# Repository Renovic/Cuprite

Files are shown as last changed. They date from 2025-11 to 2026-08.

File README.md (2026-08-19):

# Cuprite

160mm^3 High speed corexy

Cuprite_V2_2026-Jun-14_01-05-33AM-000_CustomizedView40187612621_png



* [Design Components](#design-components)
* [Design Reasoning](#why-did-i-design-this)
* [BOM](<BOM.csv>)
* [Graphs](#graphs)

## Files
- [CAD (F3Z)](CAD/Cuprite.f3z)
- [CAD (STEP)](CAD/Cuprite.step)
- [PCB Gerbers](PCB/Cuprite_ADXL_gerbers.zip)
- [BOM](<BOM.csv>)

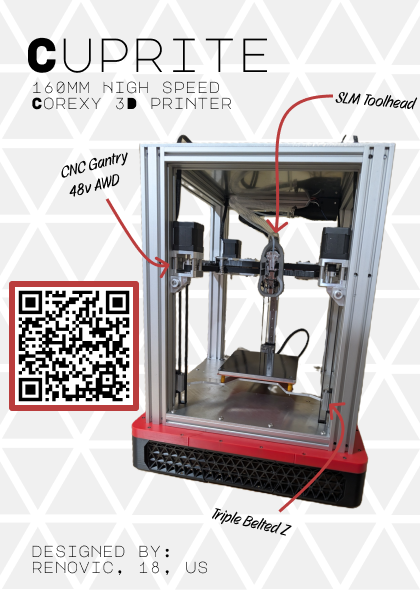
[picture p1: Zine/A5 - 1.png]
A5 - 1


### Sponsors
* [Hack Club (Fallout)](https://fallout.hackclub.com/) 
* [Sunlu](https://www.sunlu.com/)
* [OSHWLAB(JLCPCB)](https://oshwlab.com/activities/stars)
* [LDO](https://ldomotion.com/)
* [BST Automation](https://www.bstautomation.com/)
* [Filastruder](https://www.filastruder.com/)

## Design Components
- Fast and Rigid Corexy Gantry
  * Monolith Inspired gantry
  * 12mm AWD using 2504 s55 nema 17s, with 48V
  * Full cnc components for rigidity and reduced mass
- Solid Frame
  * 4040 verticals and 2040/4040 horizontals
  * 5mm structural aluminum panels
- Triple Z Axis
  * Triple Nema 17 G2Z
  * 9mm Belts
  * Maxwell motion coupling for accurate bed leveling (Inspired by ANNEX K3 Z)
- Rigid Toolhead 
  * CNC and SLM toolhead
  * Custom hotend for a cheap long meltzone (~55mm)
  * Center of mass optimized
  * Duct design aided by CFD
- Aesthetic panels
  * Parametric Kumiko panels that allow for customizability
  * Covers up 1/2" of PIR insulation
  * Integrates an extrusion based door

## Why did I design this?
The original concept for Cuprite was an extremely high speed corexy that focused on rigidity and made as little comrpromises as possible. Other than the build volume and size. Surprisingly, it's larger than a P1S while having a 100mm smaller bed.

The original one was a rushed design that happened in 2 weeks last summer, but it taught me a lot about printer design and I managed to get some sponsors. Now, I'm incorporating everything I've learned about good 3d printer design. 

Also, I thought the original was a bit boring with plain aluminum panels.

## What could you use from this project?
My build is pretty unique, so I dont expect people to build a similar printer, however you could utilize multiple aspects from it:
- The toolhead is afaik the most compact com optimized toolhead with a 50mm long meltzone. It about 10mm shorter than other similar toolheads.
- Kumiko panels is parametric, so you can use it on a lot of printers (not that reliable, so you might need to ask me for help with specific configurations)
- G2Z drives and Z joints. Normally G2Z drives are used on v2s or microns, but not that often on trident-like printers
- You could use my gantry since it supports 12mm belts (Monolith cnc gantry is a great option otherwise)

## Wiring?
The LDO leviathan + extension board has enough ports for all of the components, so its simply pluging into the correct ports. The only other wiring is ssrs for heatbed and chamber heater.

## Graphs




## Inspiration/References:
- Monolith Gantry: https://github.com/Monolith3D/Monolith_Gantry
- Paper View's Kumiko Panels: https://makerworld.com/en/models/1614814-large-kumiko-frame-generator#profileId-1733448
- DK's toolhead: https://github.com/Kizime123/DKs-Monolith-Toolhead
- DDerg's cnc joints: https://github.com/dderg (no project link)
- Galileo2: https://github.com/JaredC01/Galileo2
- Scarecrow for fan information and CAD: https://github.com/Thescarecow/130K-RPM-28mm-ducted-fan-Cad-COM
- Hex-Zero for Z tensioner: https://github.com/Alexander-T-Moss/Hex-Zero
- Chamber Heater Mount: https://github.com/GiulianoM/PTC_Heater_Mount
- ADXL: https://github.com/xbst/KUSBA-PRO
- LED Strip Holder: https://www.printables.com/model/84735-led-strip-holder-for-voron-24
- Also big thanks to anyone who provided feedback on any of my designs

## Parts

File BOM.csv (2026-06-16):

Category | Have/Exclude | Component / Item | Qty | Est. USD | Est. Total | Notes | Sources |  | Additional Notes
Filament
Filament | TRUE | Sunlu Black ABS | 2 |  |  | Sponsored by Sunlu
Filament | TRUE | Sunlu Red ABS | 1 |  |  | Sponsored by Sunlu
Category | Have/Exclude | Component / Item | Qty | Est. USD | Est. Total | Notes | Sources |  | Additional Notes
Frame
T-Slot | FALSE | 4040 460mm | 4 | $12.65 | $50.60 |  | https://us.misumi-ec.com/vona2/detail/110302684530/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
T-Slot | FALSE | 4040 290mm | 4 | $8.19 | $32.76 |  | https://us.misumi-ec.com/vona2/detail/110302684530/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
T-Slot | FALSE | 2040 290mm | 6 | $5.75 | $34.50 |  | https://us.misumi-ec.com/vona2/detail/110302684350/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
T-Slot | FALSE | 2020 160mm | 1 | $4.93 | $4.93 |  | https://us.misumi-ec.com/vona2/detail/110302683830/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
T-Slot | FALSE | 2020 250mm | 1 | $4.93 | $4.93 |  | https://us.misumi-ec.com/vona2/detail/110302683830/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
T-Slot | TRUE | 2020 460mm | 2 |  | $0.00 |  | https://us.misumi-ec.com/vona2/detail/110302683830/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
T-Slot | TRUE | 2020 290mm | 2 |  | $0.00 |  | https://us.misumi-ec.com/vona2/detail/110302683830/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
T-Slot | FALSE | 2010 330mm | 2 | $6.22 | $12.44 | https://www.aliexpress.us/item/3256805640390934.html
Aluminum Panels | FALSE | Structural Panels | 5 | $43.02 | $215.12 | 50% off from OSHCUT incl shipping |  | https://app.oshcut.com/cart/O-096f8b5f-96be-4d21-93b8
Panels | FALSE | Acrylic Panels | 3 | $51.46 | $154.37 | JLC | https://jlccnc.com/cnc-machining-quote
Insulation | FALSE | PIR Foam | 1 | $14.15 | $14.15 |  | https://www.menards.com/main/building-materials/insulation/foam-board-insulation/johns-manville-4-x-8-foil-faced-polyiso-foam-board-insulation/90034729/p-1444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
Rubber Feet | FALSE | Rubber Feet 28 x 22 x 16.5mm | 4 | $0.98 | $3.90 |  | https://www.aliexpress.us/item/2255800401618330.html?curPageLogUid=PIKSxm5qJwdM
Foam Tape | FALSE | Neoprene Rubber Strip | 1 | $3.21 | $3.21 |  | https://www.aliexpress.us/item/3256805075652387.html
Category | Have/Exclude | Component / Item | Qty | Est. USD | Est. Total | Notes | Sources |  | Additional Notes
Gantry
Rails | TRUE | Mgn 12 220mm | 1 |  |  | Sponsored by BST
Rails | TRUE | Mgn 9 210mm | 2 |  |  | Sponsored by BST
Tube | FALSE | 2020x3mm 250mm Tube | 1 | $14.60 | $14.60 |  | https://www.aliexpress.us/item/3256808551971726.html?curPageLogUid=GSkYAb7nQiv1
Motors | TRUE | 2504 s55 | 4 | $28.00 | $0.00 | Sponsored by LDO | https://kb-3d.com/store/stepper-motors-servos/2604-ldo-stepper-motor-high-temp-nema-17-42sth48-2504ah-s55-speedy-power-1651971790699.html
Belt | FALSE | 12mm belt 2.4M | 1 | $18.99 | $18.99 |  | https://diodekingsupply.com/products/gates-power-grip-gt2-epdm-belt-2-4-meter-closed-loop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 |  | 1121mm for 1 belt length
Pulleys | FALSE | Gt2 20t 12mm | 8 | $3.47 | $27.78 |  | https://www.aliexpress.us/item/2251832836965041.html
Pulleys | FALSE | Gt2 20t 6mm | 4 | $3.06 | $12.23 |  | https://www.aliexpress.us/item/2251832836965041.html
Bearings | FALSE | f605 | 20 | $0.37 | $7.40 | JLC | https://jlcmc.com/product/b/C15/BR8366/deep-groove-ball-bearings-with-flange-types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
Bearings | FALSE | 605 bearing | 6 | $0.15 | $0.91 | JLC | https://jlcmc.com/product/b/C15/BR8364/deep-groove-ball-bearing-double-side-with-dust-cover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
Bearings | FALSE | f695 | 4 | $0.20 | $0.80 | JLC | https://jlcmc.com/product/b/C15/BR8366/deep-groove-ball-bearings-with-flange-types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
Spacer | FALSE | M3xD6x20mm | 14 | $0.51 | $7.15 |  | https://www.aliexpress.us/item/3256807676471039.html
Spacer | FALSE | M5xD8x5mm | 20 | $0.20 | $4.03 |  | https://www.aliexpress.us/item/3256807676471039.html
Pin | FALSE | M3xD6x35mm | 6 | $0.74 | $4.44 |  | https://www.aliexpress.us/item/3256803877489650.html
Pin | FALSE | 5mmx40mm | 4 | $0.71 | $2.85 |  | https://www.aliexpress.us/item/3256806837028480.html
Shims | FALSE | 0.5mm 5ID | 16 | $0.12 | $1.94 |  | https://www.aliexpress.us/item/3256801859874107.html
Shims | FALSE | 1mm 5ID | 6 | $0.35 | $2.11 |  | https://www.aliexpress.us/item/3256801859874107.html
Spring | FALSE | 6mm OD 9mm Length | 4 | $0.33 | $1.32 | JLC | https://www.aliexpress.us/item/3256805126221346.html?gatewayAdapt=glo2usa4itemAdapt
CNC parts | FALSE | Rear Motor Mounts | 4 | $26.52 | $106.08 | JLC | https://jlccnc.com/cnc-machining-quote
CNC parts | FALSE | Front Motor Mounts | 4 | $25.61 | $102.42 | JLC | https://jlccnc.com/cnc-machining-quote
CNC parts | FALSE | Tensioners | 2 | $17.54 | $35.08 | JLC | https://jlccnc.com/cnc-machining-quote
CNC parts | FALSE | XY Joints | 4 | $32.47 | $129.88 | JLC | https://jlccnc.com/cnc-machining-quote
Category | Have/Exclude | Component / Item | Qty | Est. USD | Est. Total | Notes | Sources |  | Additional Notes
Toolhead
Heater | FALSE | STDv6 Heaters | 1 | $19.43 | $19.43 |  | https://trianglelab.net/products/std6?VariantsId=11907
Heat Break | FALSE | E3 S1 Bimetallic heatbreak | 1 | $5.70 | $5.70 |  | https://www.aliexpress.us/item/3256805790699617.html
CPAP | FALSE | 130k RPM Fan | 1 | $13.86 | $13.86 |  | https://www.aliexpress.us/item/3256808315658138.html?gatewayAdapt=glo2usa4itemAdapt
CPAP | FALSE | CPAP Tube | 1 | $7.00 | $7.00 |  | https://www.ebay.com/itm/197951054068?itmmeta=01KSKRKVPZHTJWCMN59X1VYEBX
Gears | FALSE | K1 gearset | 1 | $9.07 | $9.07 |  | https://www.aliexpress.us/item/3256808414846514.html
Motor | TRUE | Nema 14 | 1
Bearing | FALSE | 624ZZ | 1 | $0.10 | $0.10 | JLC | https://jlcmc.com/product/b/C15/BR8364/deep-groove-ball-bearing-double-side-with-dust-cover
Bearing | FALSE | Mr84zz | 10 | $1.01 | $10.06 |  | https://www.aliexpress.us/item/3256809175647670.html
SLM Parts | FALSE | Heatblock brace | 1 | $11.90 | $11.90
SLM Parts | FALSE | Ducts | 1 | $31.56 | $31.56
SLM Parts | FALSE | Belt Clamp | 2 | $4.00 | $8.00
SLM Parts | FALSE | Belt Clip | 2 | $4.00 | $8.00
CNC Parts | FALSE | Center Block | 1 | $86.06 | $86.06 | JLC | https://jlccnc.com/cnc-machining-quote
CNC Parts | FALSE | Extruder Housing | 1 | $39.21 | $39.21 | JLC | https://jlccnc.com/cnc-machining-quote
CNC Parts | FALSE | Hotend Block | 1 | $50.21 | $50.21 | JLC | https://jlccnc.com/cnc-machining-quote
CPAP | FALSE | Hose Clamps | 10 | $0.19 | $1.87 |  | https://www.aliexpress.us/item/3256807343760250.html
Category | Have/Exclude | Component / Item | Qty | Est. USD | Est. Total | Notes | Sources |  | Additional Notes
Z axis
Rails | TRUE | MGN12H 200mm | 3 |  |  | Sponsored by BST
Bed | TRUE | 160mm SaladFork Bed | 1
Heater | FALSE | JLC Flex heater | 1 | $20.01 | $20.01 | JLC | https://flexheater.jlcpcb.com/quote
G2z | FALSE | G2z Kits | 2 | $39.99 | $79.98 | Filastruder
Belt | FALSE | 9mm 2m | 1 | $23.80 | $23.80 | Filastruder | https://www.filastruder.com/collections/gates/products/gates-2gt-belts-high-temperature-epdm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
Pulley | FALSE | 20t Gt2 9mm Pulley 8mm ID | 3 | $5.64 | $16.92 |  | https://www.aliexpress.us/item/2255800930086012.html
Pin | FALSE | 8x45mm M5 | 3 | $1.72 | $5.16 | JLC | https://jlcmc.com/product/s/B08/BACD/linear-shaft-solid-straight-one-end-with-internal-thread-g6-tolerance
Spring | TRUE | Bed Springs | 3
Bearing | FALSE | MR148ZZ | 6 | $0.18 | $1.11 | JLC | https://jlcmc.com/product/b/C15/BR8364/deep-groove-ball-bearing-double-side-with-dust-cover
Shims | FALSE | 0.5mm 8ID | 9 | $0.24 | $2.17 |  | https://www.aliexpress.us/item/3256801859874107.html?mp=1
SLM Parts | FALSE | Belt Clamp | 3 | $4.00 | $12.00 |  | https://jlc3dp.com/3d-printing-quote
SLM Parts | FALSE | Z Joints | 3 | $11.05 | $33.15 | JLC | https://jlc3dp.com/3d-printing-quote
CNC Parts | FALSE | Z Idlers | 3 | $21.68 | $65.04 | JLC | https://jlccnc.com/cnc-machining-quote
Category | Have/Exclude | Component / Item | Qty | Est. USD | Est. Total | Notes | Sources |  | Additional Notes
Kumiko Panels
Magnets | TRUE | 6x3mm | 12
Pin | TRUE | 5mm x100mm | 1 | $1.52 | $0.00
Pin | FALSE | 5mm x 50mm | 2 | $1.69 | $3.38 | JLC | https://jlcmc.com/product/s/B08/BACA/linear-shaft-solid-straight-g6-tolerance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
Bushing | FALSE | 9x8mm Bushing 5ID | 6 | $0.79 | $4.71 | JLC | https://jlcmc.com/product/s/B01/BWYA/oil-free-bushing-special-bronze-straight-column-inner-diameter-tolerance-f7-e7-outer-diameter-tolerance-m6-r6
Shim | TRUE | 0.5mm shim 5ID | 6
Category | Have/Exclude | Component / Item | Qty | Est. USD | Est. Total | Notes | Sources |  | Additional Notes
Fasteners
BHCS | FALSE | M5x45 BHCS | 4 | $0.16 | $0.66 | JLC | https://jlcmc.com/product/s/E02/EDLG/iso-7380-hex-socket-button-head-screw
BHCS | FALSE | M5x40 BHCS | 6 | $0.09 | $0.52 | JLC | https://jlcmc.com/product/s/E02/EDLG/iso-7380-hex-socket-button-head-screw
BHCS | FALSE | M5x30 BHCS | 8 | $0.04 | $0.34 | JLC | https://jlcmc.com/product/s/E02/EDLG/iso-7380-hex-socket-button-head-screw
BHCS | FALSE | M5x16 BHCS | 32 | $0.03 | $0.83 | JLC | https://jlcmc.com/product/s/E02/EDLG/iso-7380-hex-socket-button-head-screw
BHCS | FALSE | M5x10 BHCS | 87 | $0.02 | $1.48 | JLC | https://jlcmc.com/product/s/E02/EDLG/iso-7380-hex-socket-button-head-screw
BHCS | FALSE | M5x8 BHCS | 55 | $0.02 | $1.01 | JLC | https://jlcmc.com/product/s/E02/EDLG/iso-7380-hex-socket-button-head-screw
BHCS | FALSE | M4x20 BHCS | 8 | $0.02 | $0.16 | JLC | https://jlcmc.com/product/s/E02/EDLG/iso-7380-hex-socket-button-head-screw
BHCS | FALSE | M4x8 BHCS | 4 | $0.02 | $0.09 | JLC | https://jlcmc.com/product/s/E02/EDLG/iso-7380-hex-socket-button-head-screw
BHCS | FALSE | M3x25 BHCS | 32 | $0.01 | $0.46 | JLC | https://jlcmc.com/product/s/E02/EDLG/iso-7380-hex-socket-button-head-screw
BHCS | FALSE | M3x20 BHCS | 16 | $0.01 | $0.19 | JLC | https://jlcmc.com/product/s/E02/EDLG/iso-7380-hex-socket-button-head-screw
BHCS | FALSE | M3x12 BHCS | 16 | $0.01 | $0.12 | JLC | https://jlcmc.com/product/s/E02/EDLG/iso-7380-hex-socket-button-head-screw
BHCS | FALSE | M3x10 BHCS | 32 | $0.01 | $0.23 | JLC | https://jlcmc.com/product/s/E02/EDLG/iso-7380-hex-socket-button-head-screw
BHCS | FALSE | M3x8 BHCS | 35 | $0.01 | $0.20 | JLC | https://jlcmc.com/product/s/E02/EDLG/iso-7380-hex-socket-button-head-screw
BHCS | FALSE | M3x6 BHCS | 63 | $0.01 | $0.33 | JLC | https://jlcmc.com/product/s/E02/EDLG/iso-7380-hex-socket-button-head-screw
SHCS | FALSE | M5x45 SHCS | 4 | $0.11 | $0.44 | JLC | https://jlcmc.com/product/s/E02/EDLA/din-912-gb-t-70.1-standard-socket-head-cap-screws-full---half-thread
SHCS | FALSE | M4x12 SHCS | 6 | $0.02 | $0.12 | JLC | https://jlcmc.com/product/s/E02/EDLA/din-912-gb-t-70.1-standard-socket-head-cap-screws-full---half-thread
SHCS | FALSE | M3x45 SHCS | 14 | $0.04 | $0.57 | JLC | https://jlcmc.com/product/s/E02/EDLA/din-912-gb-t-70.1-standard-socket-head-cap-screws-full---half-thread
SHCS | FALSE | M3x40 SHCS | 3 | $0.07 | $0.21 | JLC | https://jlcmc.com/product/s/E02/EDLA/din-912-gb-t-70.1-standard-socket-head-cap-screws-full---half-thread
SHCS | FALSE | M3x35 SHCS | 2 | $0.05 | $0.09 | JLC | https://jlcmc.com/product/s/E02/EDLA/din-912-gb-t-70.1-standard-socket-head-cap-screws-full---half-thread
SHCS | FALSE | M3x30 SHCS | 12 | $0.03 | $0.34 | JLC | https://jlcmc.com/product/s/E02/EDLA/din-912-gb-t-70.1-standard-socket-head-cap-screws-full---half-thread
SHCS | FALSE | M3x20 SHCS | 64 | $0.02 | $1.17 | JLC | https://jlcmc.com/product/s/E02/EDLA/din-912-gb-t-70.1-standard-socket-head-cap-screws-full---half-thread
SHCS | FALSE | M3x16 SHCS | 4 | $0.02 | $0.10 | JLC | https://jlcmc.com/product/s/E02/EDLA/din-912-gb-t-70.1-standard-socket-head-cap-screws-full---half-thread
SHCS | FALSE | M3x12 SHCS | 4 | $0.02 | $0.08 | JLC | https://jlcmc.com/product/s/E02/EDLA/din-912-gb-t-70.1-standard-socket-head-cap-screws-full---half-thread
SHCS | FALSE | M3x10 SHCS | 20 | $0.01 | $0.22 | JLC | https://jlcmc.com/product/s/E02/EDLA/din-912-gb-t-70.1-standard-socket-head-cap-screws-full---half-thread
SHCS | FALSE | M3x8 SHCS | 8 | $0.01 | $0.11 | JLC | https://jlcmc.com/product/s/E02/EDLA/din-912-gb-t-70.1-standard-socket-head-cap-screws-full---half-thread
FHCS | FALSE | M3x25 FHCS | 50 | $0.01 | $0.70 | JLC | https://jlcmc.com/product/s/E02/EDLJ/din-7991-gb-t-70.3-hex-socket-countersunk-head-screw
FHCS | FALSE | M3x20 FHCS | 32 | $0.01 | $0.35 | JLC | https://jlcmc.com/product/s/E02/EDLJ/din-7991-gb-t-70.3-hex-socket-countersunk-head-screw
FHCS | FALSE | M3x10 FHCS | 6 | $0.01 | $0.04 | JLC | https://jlcmc.com/product/s/E02/EDLJ/din-7991-gb-t-70.3-hex-socket-countersunk-head-screw
FHCS | FALSE | M3x8 FHCS | 9 | $0.01 | $0.06 | JLC | https://jlcmc.com/product/s/E02/EDLJ/din-7991-gb-t-70.3-hex-socket-countersunk-head-screw
FHCS | FALSE | M3x6 FHCS | 16 | $0.00 | $0.07 | JLC | https://jlcmc.com/product/s/E02/EDLJ/din-7991-gb-t-70.3-hex-socket-countersunk-head-screw
Low profile SHCS | FALSE | M3x8 SHCS Low | 2 | $0.79 | $1.59 | JLC | https://jlcmc.com/product/s/E02/EDLZ/hex-socket-cap-screw-ultra-short-head-type
Shoulder Bolt | FALSE | M3 D4x12 Shoulder | 2 | $0.00 | #REF! | JLC
Set Screw | FALSE | M2.5x2.5 set screw | 1 | $0.09 | $0.09 | JLC | https://jlcmc.com/product/s/E02/EDLR/din-913-914-915-916-hex-socket-set-screw-(flat-cone-cup-point-end)
Set Screw | FALSE | M4x4 set screw | 1 | $0.01 | $0.01 | JLC | https://jlcmc.com/product/s/E02/EDLR/din-913-914-915-916-hex-socket-set-screw-(flat-cone-cup-point-end)
Set Screw | FALSE | M4x3 set screw | 8 | $0.01 | $0.05 | JLC | https://jlcmc.com/product/s/E02/EDLR/din-913-914-915-916-hex-socket-set-screw-(flat-cone-cup-point-end)
Heatset | FALSE | M3 Heatset | 70 | $0.07 | $4.70 |  | https://www.aliexpress.us/item/3256805885174058.html
Hex Nut | FALSE | M5 Hex nut | 8 | $0.11 | $0.91 | JLC | https://jlcmc.com/product/s/E04/EMLC/anti-loosening-nut
Hex Nut | TRUE | M4 Hex nut | 6 | $0.00 | $0.00 | JLC | https://jlcmc.com/product/s/E04/EMLC/anti-loosening-nut
Hex Nut | TRUE | M3 Hex nut | 58 | $0.00 | $0.00 |  | https://jlcmc.com/product/s/E04/EMLC/anti-loosening-nut
Hex Nut | FALSE | M3 Hex nut (lock) | 9 | $0.15 | $1.38 | JLC | https://jlcmc.com/product/s/E04/EMLC/anti-loosening-nut
T Nut | FALSE | M5 T nut | 102 | $0.06 | $6.61 | JLC | https://jlcmc.com/product/s/T02/TPAB/m3-m4-m5-roll-in-t-slot-nut-with-ball-spring-for-20-series-aluminum-profiles
T Nut | FALSE | M3 T nut | 82 | $0.07 | $5.39 | JLC | https://jlcmc.com/product/s/T02/TPAB/m3-m4-m5-roll-in-t-slot-nut-with-ball-spring-for-20-series-aluminum-profiles
Washer | FALSE | M5 | 100 | $0.00 | $0.29 | JLC | https://jlcmc.com/product/s/E06/EPDA/flat-washer-level-a
Category | Have/Exclude | Component / Item | Qty | Est. USD | Est. Total | Notes | Sources |  | Additional Notes
Electronics
Mainboard | TRUE | LDO leviathan | 1 |  |  | Sponsored by LDO
Mainboard | FALSE | LDO leviathan Expansion | 1 |  |  | Sponsored by LDO
SBC | FALSE | RPI 5 1gb | 1 | $42.99 | $42.99 |  | https://www.microcenter.com/product/704295/raspberry-pi-5
PSU | TRUE | 24V 200W | 1 |  | $0.00
PSU | FALSE | 48V 200W | 1 | $26.99 | $26.99 | Filastruder | https://www.filastruder.com/collections/power-supplies/products/meanwell-lrs-200-48-psu
Fans | FALSE | 6025 fans | 8 | $1.70 | $13.58 | JLC
Fans | FALSE | 6015 fans | 2 | $6.89 | $13.78 |  | https://www.aliexpress.us/item/2251832744094136.html
Fans | FALSE | 8038 fans | 2 | $2.99 | $2.99 | Filastruder | https://www.filastruder.com/products/nmb-technologies-08038ra-24s-ea-axial-fan-24vdc-1-75a-42w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
SSR | TRUE | SSR | 2 | $34.00 | $0.00 | Free from TE | https://www.te.com/en/product-1-2323802-1.html
Heater | FALSE | PTC Heater | 1 | $17.90 | $17.90 |  | https://www.amazon.com/Precision-Constant-Temperature-Electric-Humidifier/dp/B07P5NCR2F/
LEDs | FALSE | 24V 2835 | 1 | $7.28 | $7.28 |  | https://www.aliexpress.us/item/3256802169002555.html?curPageLogUid=aFKuQChHYUUk
Wires | FALSE | 22 AWG FEP wire | 4 | $2.67 | $10.68 |  | https://www.aliexpress.us/item/2251832618202013.html
Wires | FALSE | 16 AWG FEP wire | 2 | $6.49 | $12.98 |  | https://www.aliexpress.us/item/2251832618202013.html
Sleeve | FALSE | PET sleeve 4mm | 1 | $5.09 | $5.09 |  | https://www.aliexpress.us/item/2251832618202013.html
Sleeve | FALSE | PET sleeve 6mm | 1 | $6.34 | $6.34 |  | https://www.aliexpress.us/item/2251832618202013.html
Connectors | FALSE | JST XH | 1 | $4.31 | $4.31 |  | https://www.aliexpress.us/item/3256808432090471.html
Connectors | FALSE | Crimp Connectors | 1 | $7.84 | $7.84 |  | https://www.aliexpress.us/item/3256809169357323.html
Crimper | FALSE | IWISS Crimper | 1 | $19.28 | $19.28 |  | https://www.aliexpress.us/item/3256809419112769.html
 | Parts Total(Shipping Included) |  | Tax | Total
AliExpress |  | $223.76 | $17.90 | $241.66
Amazon |  | $17.90 | $1.43 | $19.33
Ebay |  | $11.00 | $0.88 | $11.88
Oshcut |  | $215.12 | $17.21 | $232.33
Misumi |  | $89.40 | $10.98 | $100.38
In3dtec |  | $103.87 | $8.31 | $112.18
Trianglelab |  | $19.43 | $1.55 | $20.98
Menards |  | $14.15 | $1.13 | $15.28
Microcenter |  | $42.99 | $3.44 | $46.43
JLCPCB(Sponsor) |  | $300.00 | $24.00 | $324.00
Filastruder (Half Sponsor) |  | $78.76 | $6.30 | $85.06
Total | $1,209.52

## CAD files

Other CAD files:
CAD/Toolhead.step
CAD/Cuprite.step
CAD/Cuprite.f3z
CAD/Toolhead.f3z

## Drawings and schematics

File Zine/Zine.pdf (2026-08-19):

# Cuprite

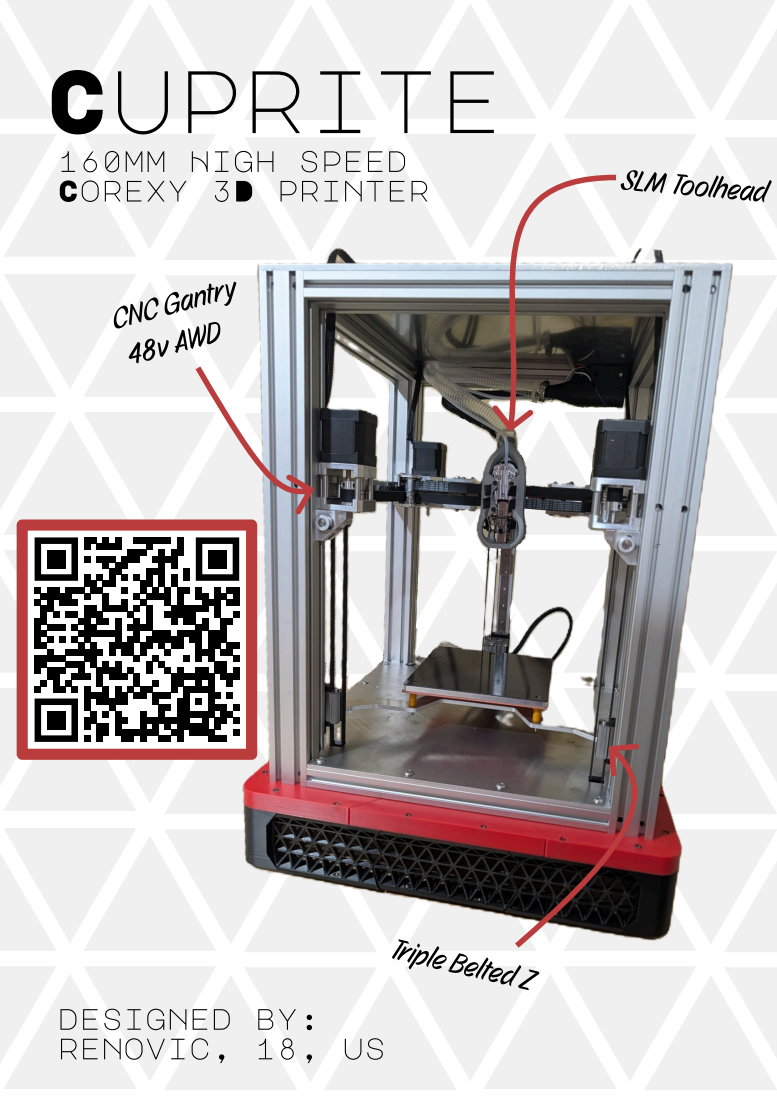
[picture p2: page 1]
CNC Gantry 48v AWD; SLM Toolhead; Triple Belted Z

160mm High speed Corexy 3D printer

designed by:
renovic, 18, us

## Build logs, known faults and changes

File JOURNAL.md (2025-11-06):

<!--
  ===================    !!READ THIS NOTICE!!   ====================
  DO NOT edit this file manually. Your changes WILL BE OVERWRITTEN!
  This journal is auto generated and updated by Hack Club Blueprint.
  To edit this file, please edit your journal entries on Blueprint.
  ==================================================================
-->

## 11/1/2025 - Intial Design Ideas, Frame, Gantry Components  

So this is a full redesign of my highway printer: 
https://github.com/Renovic/Cuprite-OLD-
Cuprite Full Printer Render(Blue)
Cuprite Electronics Render (Blue)Cuprite Toolhead Focus Render(Blue)

There are a couple of things that happened that made me want to redesign:
- Sponsors: I reached out to a couple of companies and I got some sponsors which means I needed to change a couple of parts. The companies are: LDO, Sunlu, JLCPCB(OSHWLABS), BST AUTOMATION, Filastruder
- Makerspace access: Now I have access to a makerspace and a source for sheetmetal so I have access to more manufacturing capabilities
- Better Design Ideas: My original design was rushed and wasn't ideal. For example, the toolhead COM wasn't next to the carriage, so it would lead to worse results.
- Better Aesthetics: I've gotten a lot of new ideas for improved aesthetics

# Day 1- Full Redesign Concept (Oct 1st - 3rd)
Over these few days, I consolidated my ideas on what I wanted to redesign. I also started sourcing parts for the build. 

So here are all of the changes from the old version I plan:
### Frame: 

2020 + 2040 - > 4040 verticals (JLCMC) 
- This will imporve rigidity greatly and allow for better mounting

### Insulation/Panels:

No Insulation -> 3/4" PIR Insulation
- Fits inside of the frame, which is why 4040 verticals are important

### Gantry: 

9mm belts -> 12mm EPDM (partialy sponsored by Filastruder)
2WD -> 4WD (Sponserd by LDO)
1/8" Alu sheetmetal -> CNC aluminum (JLCCNC)
2020 extrusion x-gantry -> 2030 aluminum tube
- Should allow for more rigidity
- ~30% Input Shaper gain from 9mm -> 12mm belts
- ~100% Input Shaper gain from 2WD -> AWD
- More Input Shaper gain from extra frame, and gantry rigidty

### Toolhead:

Peopoly Lancer -> Custom aluminum hotend (JLC3DP)
Fully SLM/CNC toolhead (JLC3DP & JLCNC)
G2 Extruder (LDO)
- Better extrusion from G2
- More rigidity from bottom supported hotend
- Centered COM from redesign
- higher flow rate

### Cooling:

WS7040 -> 130k RPM Ducted Fan
No flap -> Stepper motor flap 
- Cheaper
- Higher max cfm

### Z Axis

In chamber motors -> bottom-mounted motors
BMG Gear Reduction -> G2Z
3dp joints -> slm joints (JLC3DP)
No spring tension -> spring holding down bed frame to joints
Extrusion bed frame -> Laser cut aluminum frame
- More rigidity
- More travel from bottom-mounted z motors
- Better z motion consistency, and as a result better layer stacking

### Electronics

Fystec Spider -> Leviathan + Expansion board (sponsored by LDO)
tmc2209 XY motor drivers -> tmc5160 XY motor drivers (Built in to Leviathan)
24V XY -> 48V XY (Partially sponsored by Filastruder)
0 mainboard cooling -> 4x 6020 fans (JLCMC)
- Higher stepper motor speeds
- Better step control
- Can cool stepper motors

### Chamber Heater

None -> 100W Chamber Heater
- Cheap
- Allows for good chamber temps
### Aesthetic Improvements
Rear backpack -> top and bottom electronics enclosures
Exposed panels -> printed covers
Door hinges integrated into panel covers
- Displays Leviathan and good looking electronics on top
- Hides PSUs underneath
- Nicer visuals

Even with all of these improvments, the cost of new components should be cheaper than the original.

**Hours Spent: 12**
**Total: 12** 
# Day 2 - SLM Toolhead Redesign Concept (Oct 13th)
I started by designing a hotend similar to the hotend in the monolith toolhead, or DK's slm bmg toolhead. This should get high flow rates and have mounting for a bottom hotend brace.
I spent the rest of the time messing around with different extruder options, and hotend locations to find anything that could get me a good com and nice design.
The main issue was with bmg gears the gear covers the bolts mounting the main toolhead body into the mgn12h carriage. 
I also wanted to try using a g2e kit because it should give me very precise extrusion without any wood grain affect thats normally caused by double gear extruders. Although I didn't get as much as I wanted done, I was able to figure out the location of the hotend and extruder that could give me a decent center of mass, and I got some ideas of the rest of the design. 




**Hours Spent: 6**
**Total: 18** 

# Day 3 - CNC Front Motor Mounts (Oct 17th)
Main Goal for this was component was to incorperate the front extrusion brace and rigid part.
This is using the monolith belt path like before, but now for 12mm belts. 
Also I made sure to insert every fastener required so I can make sure I source all of the components and don't have any intersections. But this made it take a bit longer than how I was designed previously. 
During this day, I also found sources for the hardware required, most of the hardware like bearings, standoffs, and bolts were from JLCMC. 



**Hours Spent: 4**
**Total: 22** 

# Day 4 - New Frame & Panels (Oct 30th)
I redesigned the Frame to use 4040 verticals.
I also was able to find 3/8" aluminum panels, so I designed the aluminum panels to be mounted onto the frame.
Another thing I realized I missed on the first design is the rubber strips to reduce heat and vibration transfers from the frame to panels, so I designed those in. 
Finally I added insulation to the internal faces of the panels. 
The overall width of the printer is 50mm wider than the orignal printer, but it includes insulation.





**Hours Spent: 2.5**
**Total: 24.5* 

# Day 5 - X Axis (Oct 31st)
Today I redesigned the X axis and XY joints to use 12mm belts and 2030 Aluminum Tube. 
The XY joints are 2 part that clamp onto the mgn9h carriage and bolt into the carriage. 
Then I made the 2030 aluminum tube and mounting hardware. I also needed to add 3d printed crush blocks into the tube so I can mount the rail to the tube without worrying about bending the tube inwards. 
I also found the sources for aluminum tube, hardware and compression springs for correct spacing on the live idler joint. 







Then I wanted to see how the gantry looked, so I made a gantry assembly and put it into the frame.




**Hours Spent: 5.5**
**Total: 31**

## 11/2/2025 - Designing Rear Motor Mounts  

# Day 6 - Rear Motor Mounts (Nov 1st)
I was really confused about how to design the CNC belt tensioner for a while. But I finally had an idea to use slots to guide the tensioner, have a countersunk M3 screw to mount the tensioner bearing stack pin, and M5 bolts to clamp the tensioner in place. 

These took way longer than I expected because of the amount of hardware required for this part.







**Hours Spent: 6**
**Total: 37**  

## 11/3/2025 - Bed Assembly, Front Z drives  

# Day 7 - Bed Assembly, Front Z drives (Nov 2nd)
I started by designing the bed assembly. It uses a sheet metal carriage and some CNC components to mount the bed and 8mm rods that will be used for kinematic coupling. 



Then I designed the front Z drives that use G2Z planetary gearboxes for precise Z motion. Part of the design was making sure the part is entirely sealed so air from the chamber can't leak into the bottom electronics area. 







**Hours Spent: 6.5**
**Total: 43.5**  

## 11/5/2025 - Day 8 - Back Z drives, Tweaks to Z axis, More research  

# Day 8 - (Nov 4th)
I started with designing the rear Z drive, and this was pretty similar to the front Z drives, but mounted differently. 



Then I started thinking about how I was going to do the Z belt tensioners. Although I originally just planned on designing a belt tensioner similar to the Annex K3 z-axis tensioners, I wanted to see if there was something more compact. So I did some research and found Hex 0 had some very compact belt tensioners. 



These tensioners pressed the belt against the linear rail carriage and had one part slide to adjust tension. The Hex 0 z drives used 6mm belts and mgn7 rails, so I was a bit concerned about whether this would work. But thankfully, I found that the mgn12 rails had enough width for 9mm belts. I had to adjust the front z drive pulley location to make the belt line up with the edge of the carriage. I also added some channels for wires to come down the vertical 4040 extrusions, and go to the stepper. 



Then I went to make some tweaks to the bed carriage. I was a little concerened about the weight because I was using 3/8" thick aluminum and my original design was very beefy, so I checked and it was 400 grams. I decided to redesign it to be a little simpler and much lighter, and it ended up being 250 grams.

 



Finally, I started thinking about how I would get the most travel possible. So I measured out the toolhead length, z joint length and bed height and found that I only had 104mm of travel. The 200mm rail I have has a full travel of 150mm, so Im losing out on a lot. My two ideas so far are to raise the rod mounts on the bed assembly, to effectively drop the bed down, or redesign the z joints with the bearing further down. 

For reference: my original z joints (I have to redesign these for slm printing, different tensioner, and 9mm belts)


** Hours Spent: 5.5 **
** Total Hours: 49 **

## 11/6/2025 - Day 9 - Front Z Joint   

# Day 9 - (Nov 5th)
My main goal was to finish the z joints, but this one z joint took a lot longer than I was expecting. 
Yesterday, I found that the bed travel would be significantly limited if I went with my previous idea of the 8mm rods resting on top of the z joint rails, so I was trying to come up with a way to move the 8mm rod mount further down to increase Z travel. Eventually, I came up with a decent idea and designed it. 








With this design I should be able to get 135mm of travel, which I think is acceptable. The only way I can increase z travel after this is by decreasing the bed assembly thickness (currently 30mm), or increasing the height of the overall printer, which I don't think is worth it for an extra 15mm of travel.

I also had to adjust the bed carriage again slightly to match the new position of the 8mm rod mounts. 

The problem with this design is that I don't have a spring keeping the 8mm rod pressed against the bearings. The bed's weight will hold it down, but it is only a 160mm bed so it isn't very heavy, so I need some springs to hold it down. I wasn't sure how to implement it while designing the main part of the Z joint, so I'll try to add it next time.  

**Hours Spent: 3**
**Total Hours: 52**

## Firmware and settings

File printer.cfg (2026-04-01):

[mcu]

serial: #Find serial
restart_method:command

[printer]
kinematics: corexy
max_velocity: 600
max_accel: 25000
max_z_velocity: 30
max_z_accel: 1000
square_corner_velocity: 10

##################################
# XY Steppers
##################################

[stepper_x] 
step_pin: PB10
dir_pin: !PB11
enable_pin: !PG0
rotation_distance: 40
microsteps: 32
full_steps_per_rotation:200
endstop_pin: 

position_min: -5
position_endstop: 165
position_max: 165

homing_speed: 25
homing_retract_dist: 5
homing_positive_dir: true

[tmc5160 stepper_x]
cs_pin: PE15
spi_bus: spi4
#diag0_pin: ^!PG1
interpolate: false
run_current: 0.8
sense_resistor: 0.075
stealthchop_threshold: 0

[stepper_x1]
step_pin: PD15
dir_pin: PD14
enable_pin: !PG2
rotation_distance: 40
microsteps: 32
full_steps_per_rotation:200

[tmc5160 stepper_x1]
cs_pin: PB12
spi_bus: spi2
#diag0_pin: ^!PG3
interpolate: false
run_current: 0.8
sense_resistor: 0.075
stealthchop_threshold: 0

[stepper_y]
step_pin: PF15
dir_pin: !PF14
enable_pin: !PE9
rotation_distance: 40
microsteps: 32
full_steps_per_rotation:200
endstop_pin: 

position_min: 0
position_endstop: 170
position_max: 170

homing_speed: 25
homing_retract_dist: 5
homing_positive_dir: true

[tmc5160 stepper_y]
cs_pin: PE11
spi_bus: spi4
#diag0_pin: ^!PE10
interpolate: false
run_current: 0.8
sense_resistor: 0.075
stealthchop_threshold: 0

[stepper_y1]
step_pin: PG4
dir_pin: PE8
enable_pin: !PB0
rotation_distance: 40
microsteps: 32
full_steps_per_rotation:200

[tmc5160 stepper_y1]
cs_pin: PG5
spi_bus: spi2
#diag0_pin: ^!PE7
interpolate: false
run_current: 0.8
sense_resistor: 0.075
stealthchop_threshold: 0

##################################
# Z Steppers
##################################
## Z0 - Front Left
[stepper_z]
step_pin: PD4
dir_pin: PD3
enable_pin: !PD7
gear_ratio: 9:1
rotation_distance: 40    
microsteps: 32
endstop_pin: 
##  Z-position of nozzle (in mm) to z-endstop trigger point relative to print surface (Z0)
##  (+) value = endstop above Z0, (-) value = endstop below
##  Increasing position_endstop brings nozzle closer to the bed
##  After you run Z_ENDSTOP_CALIBRATE, position_endstop will be stored at the very end of your config
position_endstop: -0.5
## All builds use same Max Z
position_max: 100
position_min: -30
homing_speed: 8.0 # Leadscrews are slower than 2.4, 10 is a recommended max.
second_homing_speed: 3
homing_retract_dist: 3

[tmc2209 stepper_z]
uart_pin: PD5
interpolate: False
run_current: 0.6
sense_resistor: 0.110
stealthchop_threshold: 0

##  Z1 - Rear Center
##  E3-MOT Driver Spot
[stepper_z1]
step_pin: PC12
dir_pin: PC11
enable_pin: !PD2
gear_ratio: 9:1
rotation_distance: 40
microsteps: 32

[tmc2209 stepper_z1]
uart_pin: PD0
interpolate: False
run_current: 0.6
sense_resistor: 0.110
stealthchop_threshold: 0

##  Z2 - Front Right
##  E4-MOT Driver Spot
[stepper_z2]
step_pin: PC9
dir_pin: PC8
enable_pin: !PC10
gear_ratio: 9:1
rotation_distance: 40
microsteps: 32

[tmc2209 stepper_z2]
uart_pin: PA8
interpolate: False
run_current: 0.6
sense_resistor: 0.110
stealthchop_threshold: 0

##################################
# Extruder
##################################

##  E1-MOT Driver Spot
[extruder]
step_pin: PD10
dir_pin: PD9
enable_pin: !PD13
rotation_distance: 22.6789511
gear_ratio: 50:10
microsteps: 32
full_steps_per_rotation: 200   
nozzle_diameter: 0.400
filament_diameter: 1.75
heater_pin: PB15
sensor_type: Generic 3950
sensor_pin: PC1
min_temp: 10
max_temp: 270
max_power: 1.0
min_extrude_temp: 170
control = pid
pid_kp = 26.213
pid_ki = 1.304
pid_kd = 131.721

[tmc2209 extruder]
uart_pin: PD11
interpolate: false
run_current: 0.5
sense_resistor: 0.110
stealthchop_threshold: 0

##################################
# Bed
##################################

[heater_bed]
heater_pin: PB4
sensor_type: Generic 3950
sensor_pin: PC0
##  Adjust max_power so it doesn't exceed the SSR rating. The Omron G3NA-210B-DC5 SSR is rated at 4 amps without a heatsink.
##  The formula is "4 / (Wattage_of_bed_heater / Mains_voltage) = max_power"
##  If max_power is greater than 1.0, use 1.0
max_power: 0.6
min_temp: 0
max_temp: 120
control: pid
pid_kp: 58.437
pid_ki: 2.347
pid_kd: 363.769

##################################
# Probe (from LH stinger config)
##################################

[xz_dockable_probe]
dock_pin: 			# Pin wired to the Z endstop mounted on the extrusion
dock_x: 15		    	# X position of nozzle where the toolhead and probe magnets align
park_delta_x: -15		# X travel required to remove the probe from the dock (relative to dock_x)
detach_delta_x: 15		# X travel required to insert the probe into the dock  (relative to dock_x)
z_speed: 30
xy_speed:160
z_hop: 12			    # Z travel required to clear dock
#hook_commands: False 	# optional setting to disable the auto attach/detach features. Default is True

# Physical measurement references: 
#        Nozzle positioned at ~112mm from the left face of the Z pillar = G1 X0
#        Bed 0,0 = nozzle at G1 X18 Y38 
home_xy_position: 150,138 # probe coordinates 

[probe]
pin:^PA0			# Pin wired to Toolhead QuickDraw Probe   
x_offset: -32
y_offset: 0
samples: 1
sample_retract_dist: 5
samples_result: median
samples_tolerance: 0.02
samples_tolerance_retries: 3
speed: 5
lift_speed: 25

##### QD Probe Macros ####

[gcode_macro QD_home_tilt]
gcode:
    G28 lock_probe=1
    Z_TILT_ADJUST
    G28 Z
     
[gcode_macro QD_dock]
gcode:
    probe_detach force=1

[gcode_macro QD_attach]
gcode:
    probe_attach

[gcode_macro QD_latch]
gcode:
    probe_lock

[gcode_macro QD_mesh]
description: Heat bed, attach probe, home, mesh, detach probe
gcode:

    {% set BED_TEMP = params.BED_TEMP|default(0) %}
    M190 S{BED_TEMP}
    QD_home_tilt
    bed_mesh_calibrate


##################################
# Fans
##################################

[fan]
##  Part Cooling Fan
pin: PA13
kick_start_time: 0.5
off_below: 0.10

[idle_timeout]
timeout: 1800

[safe_z_home]
##  XY Location of the Z Endstop Switch
##  Update -10,-10 to the XY coordinates of your endstop pin 
##  (such as 157,305) after going through Z Endstop Pin
##  Location Definition step.
home_xy_position:-10,-10
speed:100
z_hop:10

[z_tilt]

z_positions:
    -37.087, 34.935
    227.925, 80
    197.08, 34.935
points:
    10, 5
    80, 130
    150, 5
    
speed: 200
horizontal_move_z: 10
retries: 5
retry_tolerance: 0.0075

#####################################################################
#   Macros (From Voron Config)
#####################################################################

[gcode_macro PRINT_START]
#   Use PRINT_START for the slicer starting script - PLEASE CUSTOMISE THE SCRIPT
gcode:
    M117 Homing...                 ; display message
    G28
    Z_TILT_ADJUST
    G28

    ##  Uncomment for for your size printer:
    #--------------------------------------------------------------------
    ##  Uncomment for 250mm build
    #G0 X125 Y125 Z30 F3600

    ##  Uncomment for 300 build
    #G0 X150 Y150 Z30 F3600

    ##  Uncomment for 350mm build
    #G0 X175 Y175 Z30 F3600
    #--------------------------------------------------------------------

   

[gcode_macro PRINT_END]
#   Use PRINT_END for the slicer ending script - please customise for your slicer of choice
gcode:
    # safe anti-stringing move coords
    {% set th = printer.toolhead %}
    {% set x_safe = th.position.x + 20 * (1 if th.axis_maximum.x - th.position.x > 20 else -1) %}
    {% set y_safe = th.position.y + 20 * (1 if th.axis_maximum.y - th.position.y > 20 else -1) %}
    {% set z_safe = [th.position.z + 2, th.axis_maximum.z]|min %}
    
    SAVE_GCODE_STATE NAME=STATE_PRINT_END

    M400                           ; wait for buffer to clear
    G92 E0                         ; zero the extruder
    G1 E-2.0 F3600                 ; retract filament
    
    TURN_OFF_HEATERS
    
    G90                                      ; absolute positioning
    G0 X{x_safe} Y{y_safe} Z{z_safe} F20000  ; move nozzle to remove stringing
    G0 X{th.axis_maximum.x//2} Y{th.axis_maximum.y - 2} F3600  ; park nozzle at rear
    M107                                     ; turn off fan
    
    BED_MESH_CLEAR

    # The purpose of the SAVE_GCODE_STATE/RESTORE_GCODE_STATE
    # command pair is to restore the printer's coordinate system
    # and speed settings since the commands above change them.
    # However, to prevent any accidental, unintentional toolhead
    # moves when restoring the state, explicitly set MOVE=0.
    RESTORE_GCODE_STATE NAME=STATE_PRINT_END MOVE=0

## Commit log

2026-06-14 New CAD
    [Cuprite.f3z, Cuprite.step]
2026-06-16 File Name Changes
    [BOM.csv, Cuprite BOM.csv]
